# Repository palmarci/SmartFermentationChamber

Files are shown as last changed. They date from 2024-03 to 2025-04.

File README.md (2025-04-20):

# Smart Fermentation Chamber

This is a SW + HW (and woodworking) project to create an insulated chamber with regulated temperature and humidity to perform food fermentation. This project is currently work-in-progress, please adapt the design for your needs and also make sure to double check the schematic/PCB before ordering.

## Table of contents
- [Table of contents](#table-of-contents)
- [Architecture](#architecture)
- [Firmware](#firmware)
- [PCB](#pcb)
- [Bill of materials](#bill-of-materials)
  - [Main components](#main-components)
  - [PCB parts](#pcb-parts)
- [Pictures](#pictures)
  - [Box](#box)
  - [Web server graphs](#web-server-graphs)
  - [ESP Web UI](#esp-web-ui)
- [TODOs](#todos)

## Architecture

The ESP32 gathers environmental data through sensors, evaluates it against target values, and manages the heater and humidifiers accordingly. This data is logged to a Python controller via MQTT, which generates graphs viewable through a web server. The ESP32 is configurable via a built-in web interface powered by [ESPUI](https://github.com/s00500/ESPUI). Additionally, the controller can send real-time alerts to a smartphone using the Telegram API. An optional 230V dimmer is available to regulate the heater's current based on the size of the heated space (setting is done via a potentiometer externally to the whole control circuit).

<picture>
    <source srcset="doc/architecture_dark.png"  media="(prefers-color-scheme: dark)">
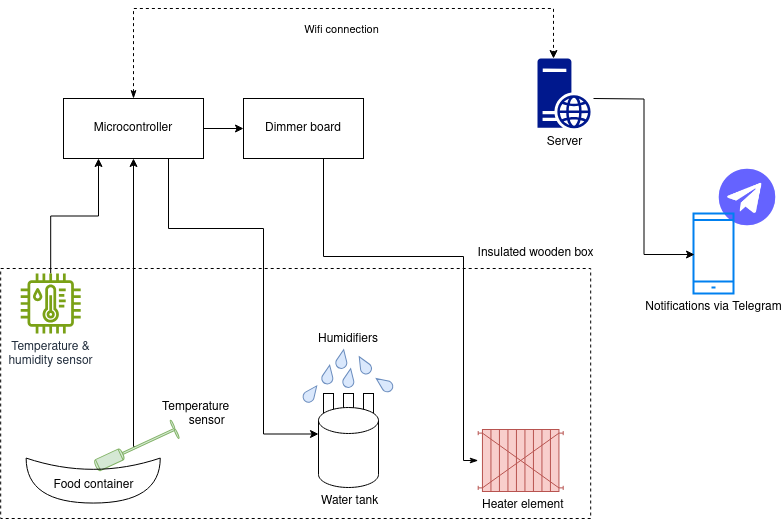
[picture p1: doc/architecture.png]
    
</picture>

## Firmware

It is a PlatformIO project. There is a [bug](https://github.com/lorol/LITTLEFS/pull/56
) in the external littlefs library, I had to fix it manually to get the FW compiling. The [fix](https://github.com/lorol/LITTLEFS/issues/43#issuecomment-1763347319
) is very easy to do.

## PCB

This is my first-ever PCB design, created in KiCad and manufactured by JLCPCB. Most of the routing was done using the auto-router, so please go easy on me. I made some mistakes, most notably I used an incorrect ESP devboard, these were fixed in 2.2, however I have not ordered those.

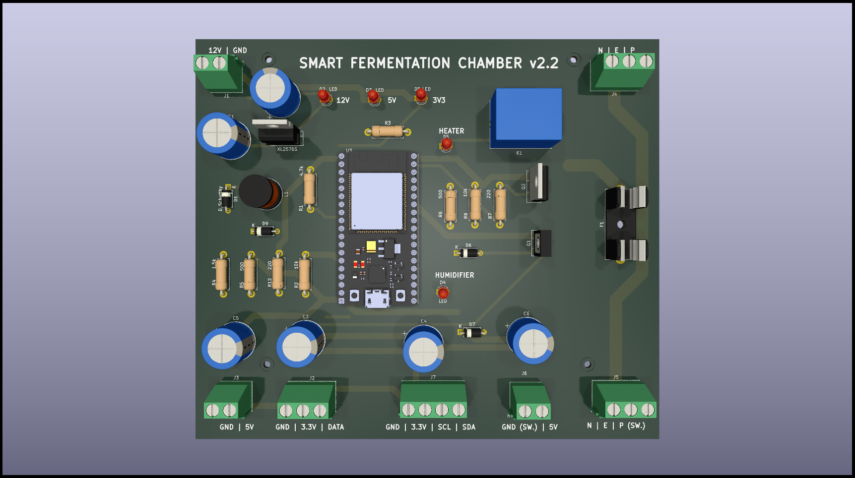
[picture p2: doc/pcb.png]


## Bill of materials

Prices are for one working unit with shipping, the date of prices is 2025.01. 
I ordered my parts from [Hestore](http://hestore.hu), if anyone needs to look up part numbers.

### Main components
|Name  |Link|Price |Description |
|---|-----|----|---|
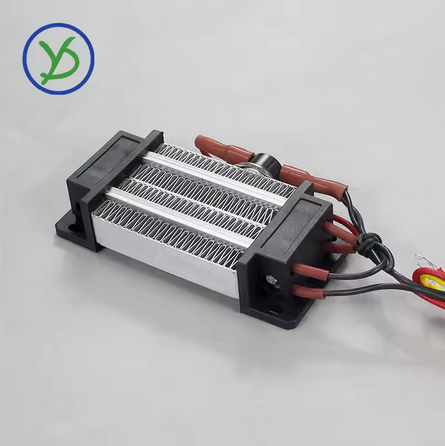
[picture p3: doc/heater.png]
|*220V 300W Incubator heater Insulation-Thermostatic PTC ceramic air heater* | https://www.aliexpress.com/item/1005007503406690.html | 12 euro | You should buy one with a fan, I added one externally!<br> |
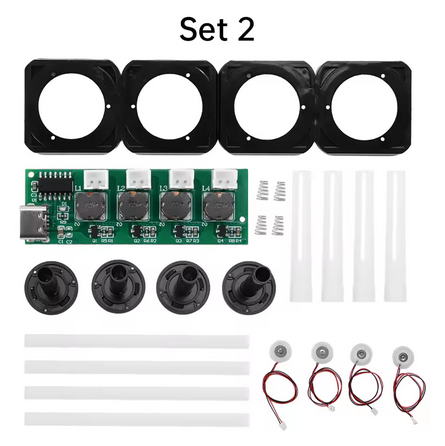
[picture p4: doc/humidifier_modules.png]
|*DC 5V Switchable Four Spray Humidifier Module Atomization Control Board DIY Ultrasonic Atomizer* | https://www.aliexpress.com/item/1005007493271175.html | 6 euro | Make sure to order one without a button, which powers on right after voltage is present<br>|
| NodeMCU ESP-32S development board | https://www.aliexpress.com/w/wholesale-nodemcu-32s.html | 6 euro | - | 
| PCB parts | - | 17 euro | *see BOM below* |
| PCB itself | https://jlcpcb.com/ | 22 euro *(for minimum order of 5 boards)* | I am not providing Gerber files, you will have to check the board/modify it if you need something, and just create the ZIP for yourself in KiCad!
| Wood + insulation | your local hardware store | max 20 euro | I don't remember the exact price
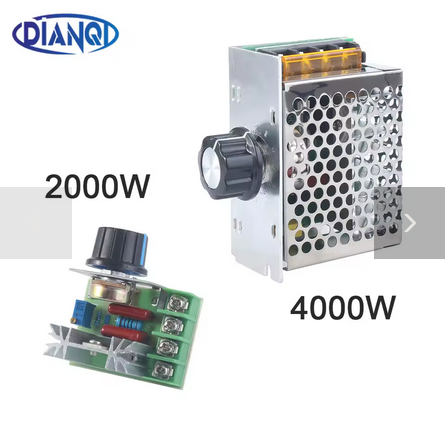
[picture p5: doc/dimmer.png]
| *2000/4000W High Power Thyristor Electronic Voltage AC 220V Regulator Dimming Speed Temperature Regulation control switch* | https://www.aliexpress.com/item/1005006015316145.html | 5 euro |  |
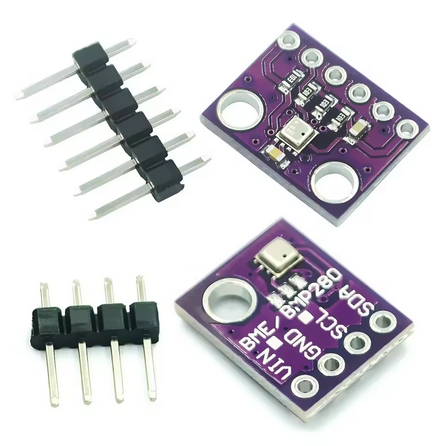
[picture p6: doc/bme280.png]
| BME280 sensor | https://www.aliexpress.com/w/wholesale-bme280-sensor.html | 4 euro |  |
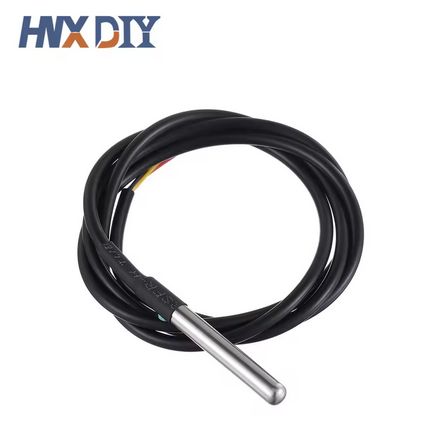
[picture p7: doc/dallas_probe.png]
| Waterproof DS18B20 Temperature Sensor | https://www.aliexpress.com/item/1005001601986600.html | 4 euro | |
| **Total** | - | **~100 euro** | + cables, wires and misc soldering stuff |

### PCB parts

|Quantity  |Item name|Description |
|---|---|---|
|6 |1000 uF / 35V|Capacitor 12.5mm/5mm |
|5 |LED 5 mm D-RD|LED |
|1 |1N4007 |Diode |
|1|	? |4.7k Resistor |
|3|	? |220R Resistor |
|2|	?| 10k Resistor |
|1|	? |1.5k Resistor |
|2|	?|500R Resistor |
|1 |? |NPN transistor |
|1 |BAT85 |Schottky-diode |
|3 |ZL262-20SG|Pin header |
|1 |IRLZ44NPBF|FET N |
|1 |SRD-5VDC-SL-C|Relay, SPDT, 5V DC, 10A / 250V AC|
|1 |330uH / 1.2A / 630mR|Inductor |
|1 |PTF/78 |Fuse holder, socket, 5x20mm|
|1 |BS232 |Fuse holder cover |
|3 | ? |PCB terminal block, 90 degrees, 0.5cm, 2-pole|
|1 | ? |PCB terminal block, 90 degrees, 0.5cm, 4-pole|
|3 | ?|PCB terminal block, 90 degrees, 0.5cm, 3-pole|
|1 |XL2576S-5.0E1|Voltage stabilizer IC, both TO220 and TO263 fit |
|3 |5X20-F-3A|Fuse, fusible, glass, fast, 5x20mm, 250V AC, 3A|

## Pictures

### Box



### Web server graphs
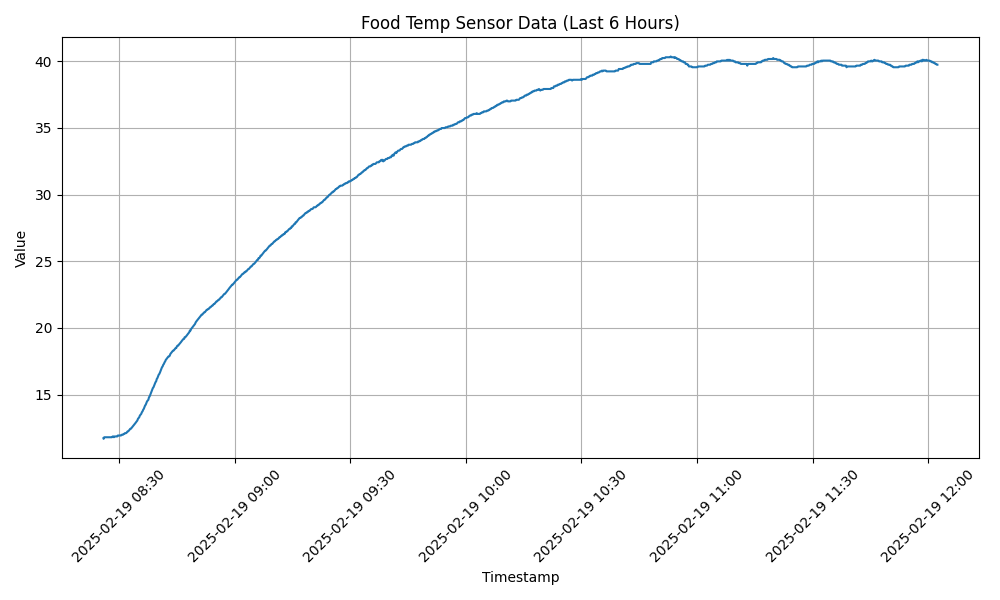
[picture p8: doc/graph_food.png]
<br>
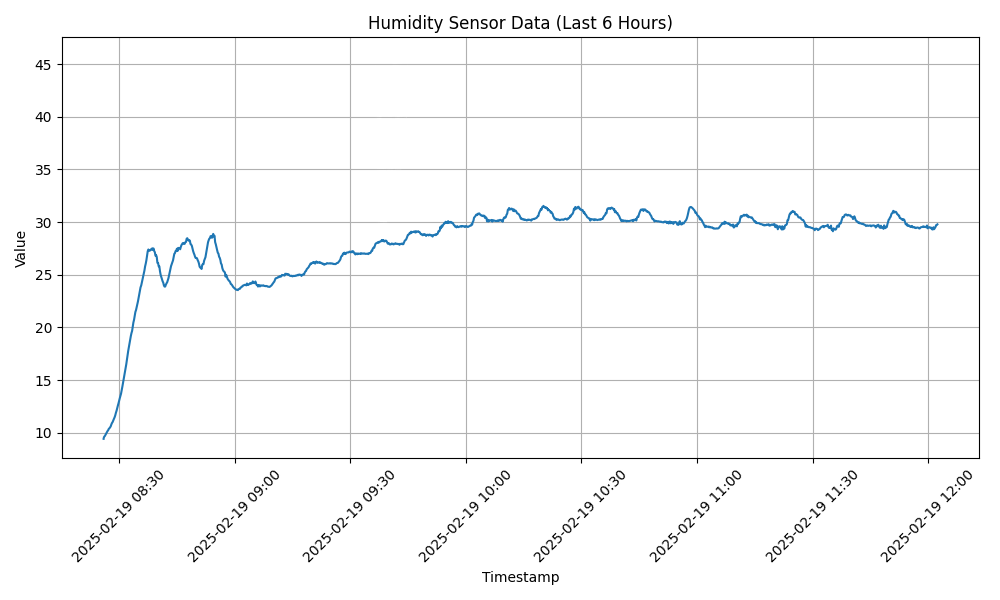
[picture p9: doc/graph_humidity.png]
<br>

### ESP Web UI
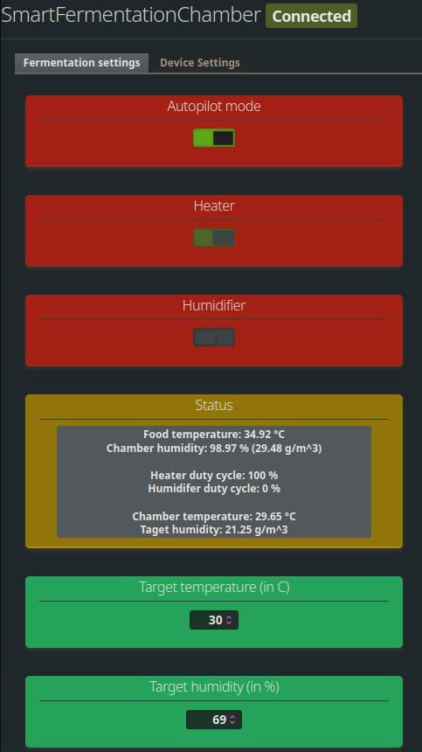
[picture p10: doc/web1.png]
<br>
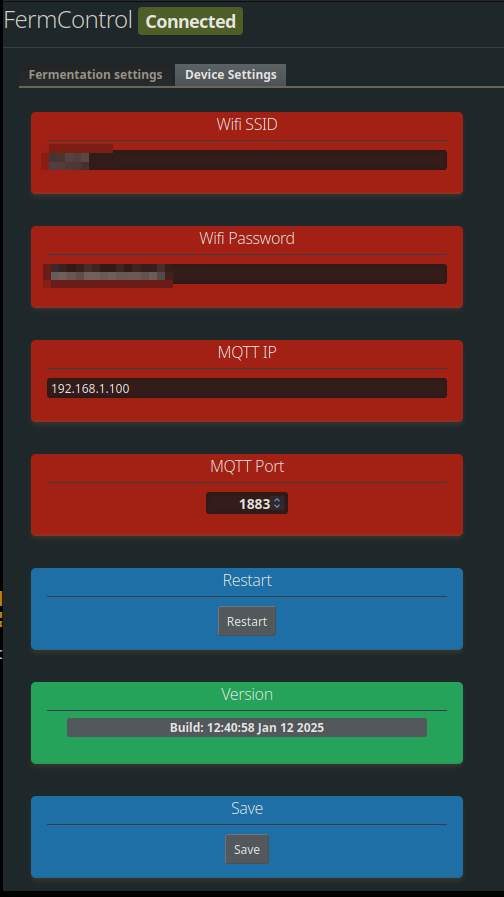
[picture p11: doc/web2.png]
<br>

## TODOs
- went hole with a steppermotor  
- hum & temp updating at the same time bug

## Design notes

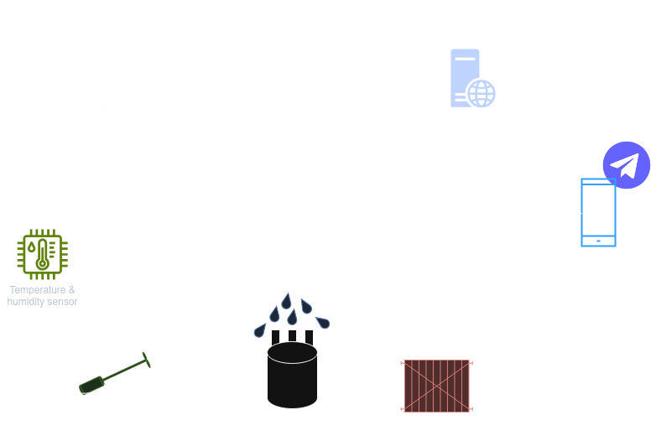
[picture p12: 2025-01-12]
doc/architecture_dark.png

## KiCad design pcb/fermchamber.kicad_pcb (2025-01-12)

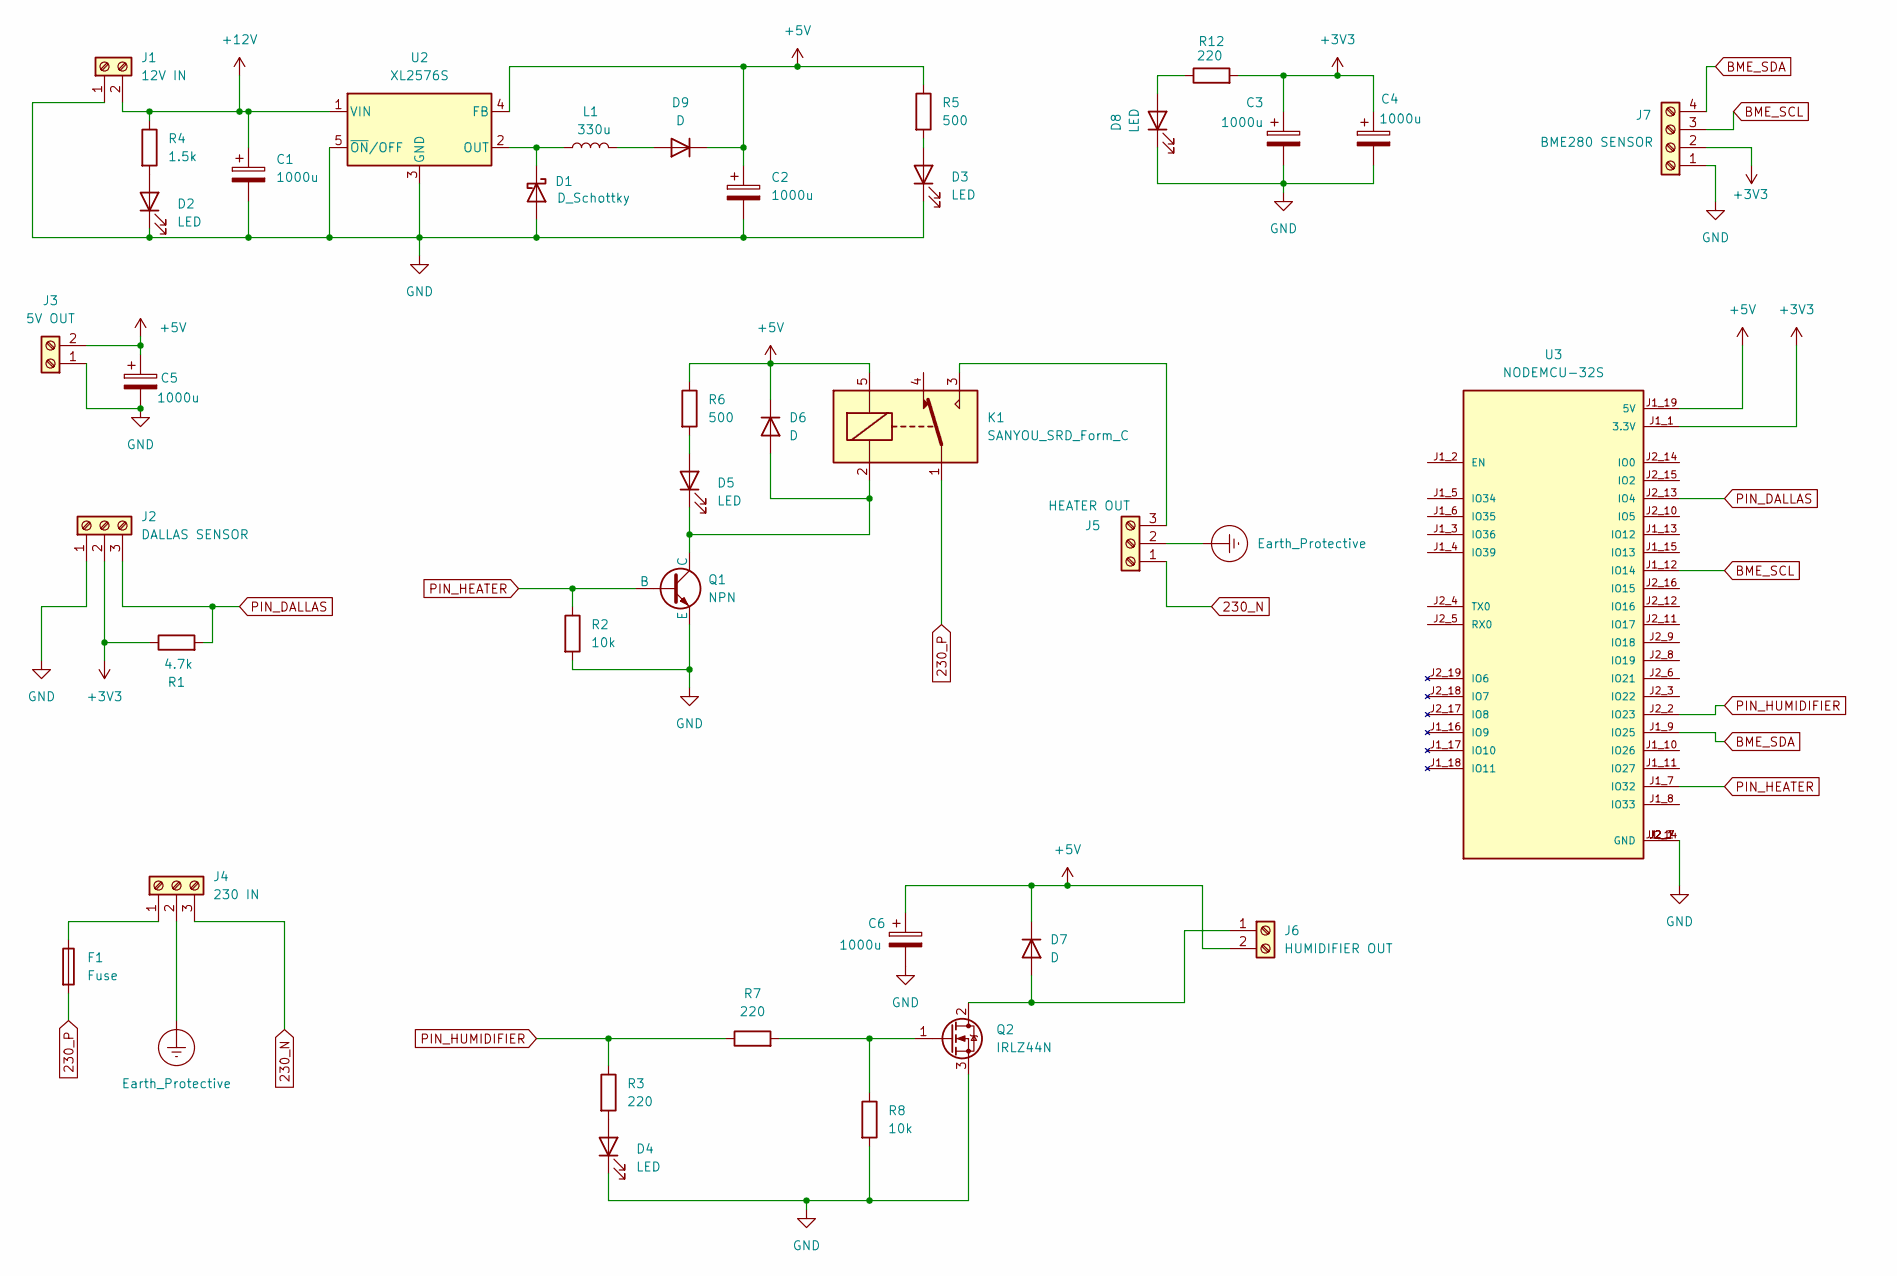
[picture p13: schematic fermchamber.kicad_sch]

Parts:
C1, C2, C3, C4, C5, C6: 1000u; CP_Radial_D12.5mm_P5.00mm
D1: D_Schottky; D_A-405_P7.62mm_Horizontal
D2, D3, D4, D5, D8: LED; LED_D3.0mm
D6, D7, D9: D; D_A-405_P7.62mm_Horizontal
F1: Fuse; Fuseholder_Cylinder-5x20mm_Schurter_0031_8201_Horizontal_Op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
J1: 12V IN; TerminalBlock_Phoenix_MKDS-1,5-2-5.08_1x02_P5.08mm_Horizont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
J2: DALLAS SENSOR; TerminalBlock_Phoenix_MKDS-1,5-3-5.08_1x03_P5.08mm_Horizont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
J3: 5V OUT; TerminalBlock_Phoenix_MKDS-1,5-2-5.08_1x02_P5.08mm_Horizont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
J4: 230 IN; TerminalBlock_Phoenix_MKDS-1,5-3-5.08_1x03_P5.08mm_Horizont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
J5: HEATER OUT; TerminalBlock_Phoenix_MKDS-1,5-3-5.08_1x03_P5.08mm_Horizont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
J6: HUMIDIFIER OUT; TerminalBlock_Phoenix_MKDS-1,5-2-5.08_1x02_P5.08mm_Horizont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
J7: BME280 SENSOR; TerminalBlock_Phoenix_MKDS-1,5-4_1x04_P5.00mm_Horizontal
K1: SANYOU_SRD_Form_C; Relay_SPDT_SANYOU_SRD_Series_Form_C
L1: 330u; L_Radial_D10.0mm_P5.00mm_Fastron_07P
Q1: NPN; TO-126-3_Vertical
Q2: IRLZ44N; TO-220-3_Vertical
R1: 4.7k; R_Axial_DIN0411_L9.9mm_D3.6mm_P12.70mm_Horizontal
R2, R8: 10k; R_Axial_DIN0411_L9.9mm_D3.6mm_P12.70mm_Horizontal
R3, R7, R12: 220; R_Axial_DIN0411_L9.9mm_D3.6mm_P12.70mm_Horizontal
R4: 1.5k; R_Axial_DIN0411_L9.9mm_D3.6mm_P12.70mm_Horizontal
R5, R6: 500; R_Axial_DIN0411_L9.9mm_D3.6mm_P12.70mm_Horizontal
U2: XL2576S; TO-220-5_Vertical
U3: NODEMCU-32S; MODULE_NODEMCU-32S; PARTREV V1

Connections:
230_N: J4.3, J5.1
230_P: F1.2, K1.1
+3V3: C3.1, C4.1, J2.2, J7.2, R1.1, R12.2, U3.J1_1 (3.3V)
+5V: C2.1, C5.1, C6.1, D6.1 (K), D7.1 (K), D9.1 (K), J3.2, J6.2, K1.5, R5.1, R6.1, U2.4 (FB), U3.J1_19 (5V)
+12V: C1.1, J1.2, R4.1, U2.1 (VIN)
BME_SCL: J7.3, U3.J1_12 (IO14)
BME_SDA: J7.4, U3.J1_9 (IO25)
Earth_Protective: J4.2, J5.2
GND: C1.2, C2.2, C3.2, C4.2, C5.2, C6.2, D1.2 (A), D2.1 (K), D3.1 (K), D4.1 (K), D8.1 (K), J1.1, J2.1, J3.1, J7.1, Q1.3 (E), Q2.3 (S), R2.2, R8.2, U2.3 (GND), U2.5 (~ON/OFF), U3.J1_14 (GND), U3.J2_1 (GND), U3.J2_7 (GND)
unnamed: D1.1 (K), L1.1, U2.2 (OUT)
unnamed: D2.2 (A), R4.2
unnamed: D3.2 (A), R5.2
unnamed: D4.2 (A), R3.2
unnamed: D5.2 (A), R6.2
unnamed: D5.1 (K), D6.2 (A), K1.2, Q1.1 (C)
unnamed: D7.2 (A), J6.1, Q2.2 (D)
unnamed: D8.2 (A), R12.1
unnamed: D9.2 (A), L1.2
unnamed: F1.1, J4.1
unnamed: J5.3, K1.3
unnamed: Q2.1 (G), R7.2, R8.1
PIN_DALLAS: J2.3, R1.2, U3.J2_13 (IO4)
PIN_HEATER: Q1.2 (B), R2.1, U3.J1_7 (IO32)
PIN_HUMIDIFIER: R3.1, R7.1, U3.J2_2 (IO23)

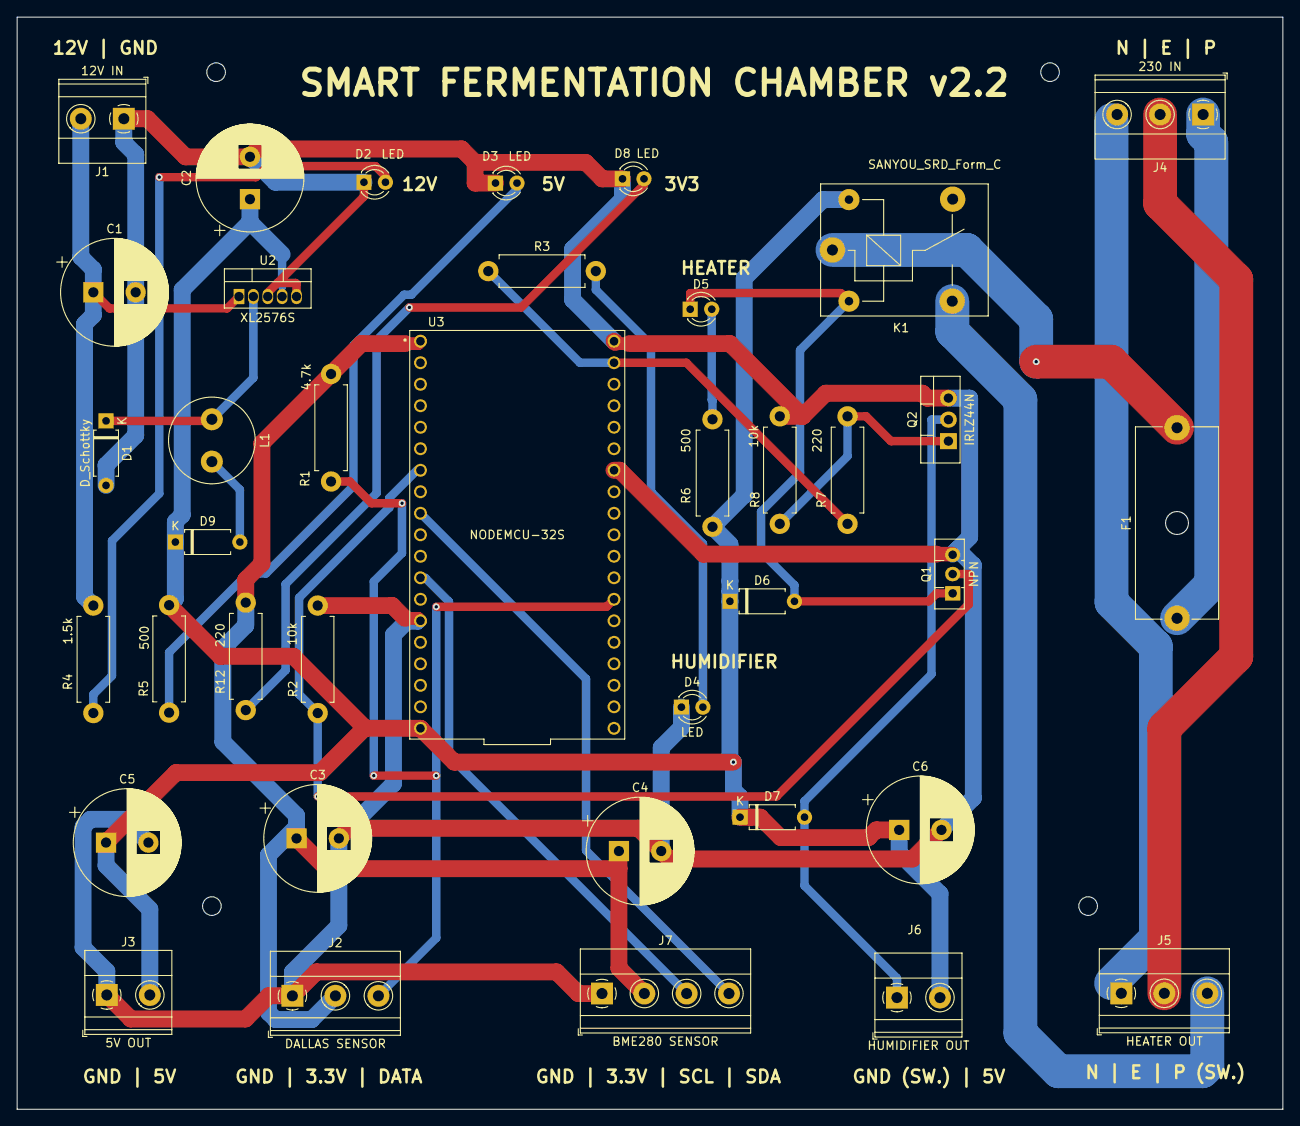
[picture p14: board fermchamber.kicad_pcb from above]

Board: 2 copper layers, 149.5 x 129.0 mm, 38 parts (0 on the bottom side), 24 nets.

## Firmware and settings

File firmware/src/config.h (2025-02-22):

#ifndef CONFIG
#define CONFIG

#include <Arduino.h>
#include "secrets.h"

// ******** PINS ********
#define LED_PIN 2 // builtin
#define ONEWIRE_BUS_PIN 4 // for the Dallas DS18B20
#define I2C_SDA_PIN 25 // for the BME280
#define I2C_SCL 14
#define PIN_HEATER 32
#define PIN_HEATER_INVERT false
#define PIN_HUMIDIFIER 23
#define PIN_HUMIDIFIER_INVERT false

// ******** COMMUNICATION ********
#define SERIAL_SPEED 115200
#define BME_I2C_ID 0x76
#define WIFI_AP_DEFAULT_IP "192.168.1.1"
#define WIFI_CONNECT_TIMEOUT 15
#define WIFI_AP_MODE_FORCE 0
#define MQTT_DEFAULT_IP "192.168.1.12"
#define MQTT_DEFAULT_PORT 1883
#define MQTT_LOG_TOPIC "log"
#define MQTT_MEASUREMENT_TOPIC "measurement"
#define MQTT_HEARTBEAT_TOPIC "heartbeat"

// ******** NVM KEY VALUES ********
// THESE MUST BE SMALLER THAN 15 CHARS !!!
#define NVM_KEY "SFCH"
#define NVM_WIFI_SSID "WIFI_SSID"
#define NVM_WIFI_PW "WIFI_PW"
#define NVM_MQTT_IP "MQTT_IP"
#define NVM_MQTT_PORT "MQTT_PORT"
#define NVM_TARGET_TEMP "NVM_T_TEMP"
#define NVM_TARGET_HUM_REL "NVM_T_HUM_REL"
#define NVM_TARGET_HUM_ABS "NVM_T_HUM_ABS"

// ******** MEASUREMENT ********
#define INVALID_MINIMUM_TEMP 0
#define INVALID_MAX_TEMP 80
#define DEFAULT_TARGET_HUMIDITY_REL 70
#define DEFAULT_TARGET_HUMIDITY_ABS 21
#define DEFAULT_TARGET_TEMP 30
#define BME_HUMIDITY_OFFSET 0.0 // these can be negative
#define BME_TEMP_OFFSET 0
#define DALLAS_TEMP_OFFSET 0.8
#define SENSOR_MEASURE_PERIOD 10 // seconds
#define SENSOR_MEASUREMENT_TIMEOUT (SENSOR_MEASURE_PERIOD * 4)
#define RELAY_PROTECTION_DELAY 1 // mins
#define DUTY_CYCLE_LOGGING_TIME 60 // mins
#define PREDICTOR_PERCENTAGE 0.04f //TODO: add this to webgui
#define PREDICTOR_AVERAGE_COUNT 5
#define PREDICTOR_ENABLED false
#define OTA_ENABLED false

// ******** SYSTEM ********
#define HOSTNAME "SmartFermentationChamber"
#define MAX_TASK_HANDLES 10
#define RESTART_AFTER_HOURS 1176 // crude overflow hack  this is 49 days if for some reason we are still alive after that
#define AUTOPILOT_ENABLED_AT_STARTUP true 
#define DISABLE_BROWNOUT false // if usb port voltage dips below 5V
#define STACK_SIZE 20000

// ******** MACROS ********
#define LOG_DEBUG 1
#define LOG_WARNING 2
#define LOG_PANIC 3
#define VERSION ("Build: " + String(__DATE__) + " " + String(__TIME__))

#endif /* CONFIG */

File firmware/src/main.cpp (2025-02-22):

#include "utils.h"
#include "control.h"
#include "nvm.h"
#include "network.h"
#include "sensors.h"
#include "web.h"
#include "config.h"
#include "tasks.h"
#include "ota.h"

#include "soc/soc.h"
#include "soc/rtc_cntl_reg.h"

#include <LittleFS.h>

void disable_brownout()
{
	WRITE_PERI_REG(RTC_CNTL_BROWN_OUT_REG, 0);
}

void pin_init() {
	logprint("*** pin_init ***");
	pinMode(LED_PIN, OUTPUT);
	pinMode(PIN_HEATER, OUTPUT);
	pinMode(PIN_HUMIDIFIER, OUTPUT);
	set_heater(false, true);
	set_humidifier(false);
}

void serial_init() {
	logprint("*** serial_init ***");
	Serial.begin(SERIAL_SPEED);
}

void setup()
{
	if (DISABLE_BROWNOUT)
	{
		disable_brownout();
	}
	serial_init();
	pin_init();
	nvm_init();
	control_init();
	wifi_init();
	mqtt_init();
	sensors_init();
	web_init();
	ota_init();
	tasks_init();
	
	set_autopilot(AUTOPILOT_ENABLED_AT_STARTUP); //only do this after everything is alive
}

void loop()
{
	// Empty, because we're using FreeRTOS tasks
}

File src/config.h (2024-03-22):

#ifndef CONFIG
#define CONFIG

#include <Arduino.h>

// PINS
// https://randomnerdtutorials.com/esp32-pinout-reference-gpios/
#define LED_PIN 2 // builtin
#define ONEWIRE_BUS_PIN 33
#define BME_I2C_SDA_PIN 32
#define BME_I2C_SCL_PIN 25
#define RELAY_PIN_HEATER 13
#define RELAY_PIN_HUMIDIFIER 27
#define INVERT_RELAYS true
#define HUMIDIFER_PUSH_GATE 99 //TODO 

// COMMUNICATION
#define BME_I2C_ID 0x76
#define WIFI_AP_DEFAULT_IP "192.168.1.1"
#define WIFI_CONNECT_TIMEOUT 15
#define WIFI_AP_MODE_FORCE 0
#define WIFI_DEFAULT_SSID "MyWifi"
#define WIFI_DEFAULT_PW "MyPassword"

#define MQTT_DEFAULT_IP "192.168.1.100"
#define MQTT_DEFAULT_PORT 1883
#define MQTT_LOG_TOPIC "log"
#define MQTT_MEASUREMENT_TOPIC "measurement"
#define MQTT_HEARTBEAT_TOPIC "heartbeat"

// NVM KEY VALUES
#define NVM_WIFI_SSID "WIFI_SSID"
#define NVM_WIFI_PW "WIFI_PW"
#define NVM_MQTT_IP "MQTT_IP"
#define NVM_MQTT_PORT "MQTT_PORT"
#define NVM_TARGET_TEMP "NVM_TARGET_TEMP"
#define NVM_TARGET_HUM "NVM_TARGET_HUM"

// SENSORS
#define INVALID_MINIMUM_TEMP 0
#define INVALID_MAX_TEMP 80
#define DEFAULT_TARGET_HUMIDITY 80
#define DEFAULT_TARGET_TEMP 60
#define SENSOR_MEASUREMENT_TOPIC_TIMEOUT 30 //seconds

// SYSTEM
#define HOSTNAME "FermControl"
#define MAX_TASK_HANDLES 10
#define RESTART_AFTER 24 // hours
#define AUTOPILOT_ENABLED_AT_STARTUP true 
#define DISABLE_BROWNOUT true // for debugging, my pc's usb port voltage dips below 5v :(
#define STACK_SIZE 20000

// MACROS
#define LOG_DEBUG 1
#define LOG_WARNING 2
#define LOG_PANIC 3
#define VERSION "Build " + String(__DATE__) + " " + String(__TIME__)

#endif /* CONFIG */

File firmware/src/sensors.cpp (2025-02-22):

#include <Arduino.h>
#include <OneWire.h>
#include <DallasTemperature.h>
#include <Adafruit_BME280.h>
#include <Wire.h>
#include <Adafruit_Sensor.h>

#include "sensors.h"
#include "utils.h"
#include "config.h"
#include "network.h"
#include "control.h"

OneWire onewire_bus(ONEWIRE_BUS_PIN);
DallasTemperature dallas_sensors(&onewire_bus);
Adafruit_BME280 bme_sensor;

#define INVALID_DEFAULT_VALUE 999

unsigned long last_valid_timer = INVALID_DEFAULT_VALUE; // overflow is taken care of by the periodic reset task
float last_hum = INVALID_DEFAULT_VALUE;
float last_food_temp = INVALID_DEFAULT_VALUE;
float last_air_temp = INVALID_DEFAULT_VALUE;

bool validate_temp_range(float input)
{
	if (input < INVALID_MINIMUM_TEMP || input > INVALID_MAX_TEMP)
	{
		return false;
	}
	return true;
}

bool validate_hum_range(float in)
{
	if (in < 0 || in > 100)
	{
		return false;
	}
	return true;
}

void check_sensor_timeout()
{
	unsigned long now = millis();
	unsigned long limit = last_valid_timer + (SENSOR_MEASUREMENT_TIMEOUT * 1000);
	if (limit < now)
	{
		reboot("sensor data timeout reached"); // was halt() instead
	}
}

// https://gist.github.com/vsee/a51d2ebc7376bbd38f3d58c87c2b5d1b
float relative_to_abs_humidity(float temp, float hum_percentage) {
	float exponent = expf((17.67f * temp) / (temp + 243.5f)); 
	float absH = (6.112f * exponent * hum_percentage * 18.02f) / ((273.15f + temp) * 100.0f * 0.08314f);
	return absH;
}

float abs_to_relative_humidity(float temp, float absH) {
	float exponent = expf((17.67f * temp) / (temp + 243.5f)); 
	float hum_percentage = ((273.15f + temp) * 100.0f * 0.08314f * absH) / (6.112f * exponent * 18.02f);
	//logprint("abs_to_relative_humidity " + String(temp) + " C, " + String(absH) + " % -> " + String(hum_percentage));
	return hum_percentage;
}

void measure_sensors()
{
	bool all_good = true;
	check_sensor_timeout();

	float current_food_temp;
	float current_air_temp;
	float current_hum;

	// food temp
	dallas_sensors.requestTemperatures();
	current_food_temp = dallas_sensors.getTempCByIndex(0) + DALLAS_TEMP_OFFSET; // no checks here, i trust the user 
	if (!validate_temp_range(current_food_temp))
	{
		logprint("food temp read invalid: " + String(current_food_temp), LOG_WARNING);
		all_good = false;
	}
	
	// humidity
	float raw_hum = bme_sensor.readHumidity();
//	logprint("raw humidity = " + String(raw_hum));
	if (validate_hum_range(raw_hum))
	{
		current_hum = raw_hum + BME_HUMIDITY_OFFSET; // add offset only after validation, this can in theory hit the limit
		// clamp it again after offsetting
		if (current_hum > 100) {
			current_hum = 100;
		} 
		if (current_hum < 0) {
			current_hum = 0;
		}
	}
	else
	{
		logprint("humidity read invalid: " + String(raw_hum), LOG_WARNING);
		all_good = false;
	}

	// air temp
	current_air_temp = bme_sensor.readTemperature() + BME_TEMP_OFFSET; // also no checks here
	if (!validate_temp_range(current_air_temp))
	{
		logprint("air temp read invalid: " + String(current_air_temp), LOG_WARNING);
		all_good = false;
	}

	if (all_good)
	{
		last_valid_timer = millis();
		last_hum = relative_to_abs_humidity(current_air_temp, current_hum);
		//last_hum = current_hum;
		last_food_temp = current_food_temp;
		last_air_temp = current_air_temp;
		mqtt_send(String(MQTT_MEASUREMENT_TOPIC) + "/humidity", String(last_hum));
		mqtt_send(String(MQTT_MEASUREMENT_TOPIC) + "/food_temp", String(last_food_temp));
		mqtt_send(String(MQTT_MEASUREMENT_TOPIC) + "/air_temp", String(last_air_temp));
	}
	else
	{
		logprint("invalid data from sensor(s), invalidated current measurement", LOG_WARNING);
	}

}

void init_dallas()
{
	dallas_sensors.begin();
	int count = dallas_sensors.getDeviceCount();
	if (count < 1)
	{
		halt("no dallas devices found on bus", 500, 0);
	}
	logprint("found " + String(count) + " dallas sensors on bus");
	dallas_sensors.setResolution(12);
	logprint("set dallas sensor resolution to 12 bits");
}

void init_bme()
{
	logprint("initializing bme sensor...");
	Wire.end();
	Wire.begin(I2C_SDA_PIN, I2C_SCL);

	if (!bme_sensor.begin(BME_I2C_ID, &Wire))
	{
		halt("failed to initialize BME280 sensor!", 1000, 0);
	}
	else
	{
		logprint("BME280 sensor initialized successfully!");
	}
}

void sensors_init()
{
	logprint("*** sensors_init ***");
	init_dallas();
	init_bme();
	measure_sensors();

	if (INVALID_DEFAULT_VALUE == last_valid_timer)
	{
		halt("read invalid data from sensors at startup", 500, 1000);
	}
}

String get_sensor_status_text()
{
	String status_text = "Food temperature: " + String(last_food_temp) + " °C\n" +
						 "Chamber humidity: " + String(abs_to_relative_humidity(last_air_temp, last_hum)) + " % (" + String(last_hum) + " g/m^3)\n\n" + 

						 "Heater duty cycle: " + String(get_heater_duty_cycle()) + " %\n"+
						 "Humidifer duty cycle: " + String(get_humidifier_duty_cycle()) + " %\n\n"+

						 "Chamber temperature: " + String(last_air_temp)  + " °C\n"+
						 "Taget humidity: " + String(get_target_hum())  + " g/m^3\n";

	return status_text;
}

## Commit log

2024-03-12 adding todos, small fix in web update logic
    [config.h, main.cpp]
2024-03-13 adding placeholder control script; added auto restart task; added ability to kill running tasks; added invalid sensor reading last value feature;
2024-03-13 added every settings to nvm saving logic; added version into webui, updated ordering, fixed textbox enter problem
    [config.h, control.cpp]
2024-03-13 fixed build errors; formatted code
    [config.h, main.cpp, sensors.cpp]
2024-03-13 added buffering for web ui inputs; added startup alive checks for sensors; fixed nvm storing for every setting; added comments & info texts
    [config.h, control.cpp, main.cpp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]
2024-03-15 implementing control.py; adding macros & debug settings into config.h; fixing bugs
    [config.h, control.cpp, main.cpp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]
2024-03-15 moving task delays to beginning, adding gpio insertion option, fixing timer logic in control script
    [config.h, control.cpp, main.cpp]
2024-03-17 reworked autopilot enable logic, added readme
    [control.cpp, main.cpp]
2024-03-17 implemented graph generation in control script, fixed autopilot firing logic, fixed library defs in platformio config
    [config.h, control.cpp]
2025-01-02 adding pcb files and gitignore from kicad
    [fermchamber.kicad_pcb, fermchamber.kicad_sch, relays.kicad_sch]
2025-01-08 fixed capactior, inductor and, voltage ic footprint in schematic; added missing labels on the pcb; clarified and added missing items in the BOM
    [fermchamber.kicad_pcb, fermchamber.kicad_sch, relays.kicad_sch]
2025-01-12 renaming pins, adding sensor offsetting in config, adding TODOs
2025-01-12 fixing TODOs in documentation
    [config.h]
2025-01-12 changed esp board to nodemcu 32s, limited current on leds, added diode for 5v usb programming backfeed, made switched labels more clear, fixed dallas data bus pull up, added pcb holes for mounting, r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
    [fermchamber.kicad_pcb, fermchamber.kicad_sch, relays.kicad_sch]
2025-02-16 rewrote controller; bugfix in wifi communication; bugfix in nvm target handling
    [config.h, control.cpp]
2025-02-16 moved flask to background thread
2025-02-18 adding experimental pid support; switching to absolute humidity targetting; adding relay protection feature; made wifi more stable; fixed reboot crash problem; small changes in controller; cleaned an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
    [config.h, control.cpp, main.cpp]
2025-02-19 adding duty cycle measurement and graph generation; removed unnecessary pid test; implemented force heater mode;
2025-02-22 adding experimental (not working) ota and prediction support; renaming controller to web gui
    [config.h, control.cpp, main.cpp]
